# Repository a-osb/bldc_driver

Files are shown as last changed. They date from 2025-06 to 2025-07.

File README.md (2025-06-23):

# BLDC Motor Driver
  
This project aims to provide a compact and efficient solution for controlling brushless DC motors in robotics applications. It offers precise feedback and control, making it suitable for tasks that require accurate positioning and smooth motion.

Designed to be compatible with the SimpleFOC project

Based on key components
- DRV8317 integrated mosfet BLDC driver
- STM32G0 Microcontroller
- AS5047D magnetic encoder

Interfaces
- UART
- USB
- CAN

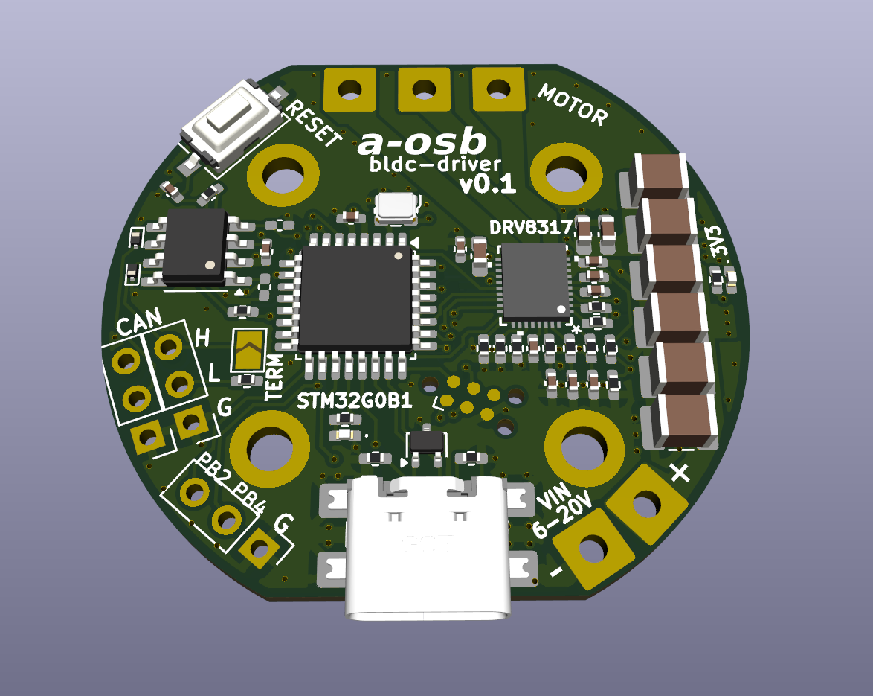
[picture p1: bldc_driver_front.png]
3D Front

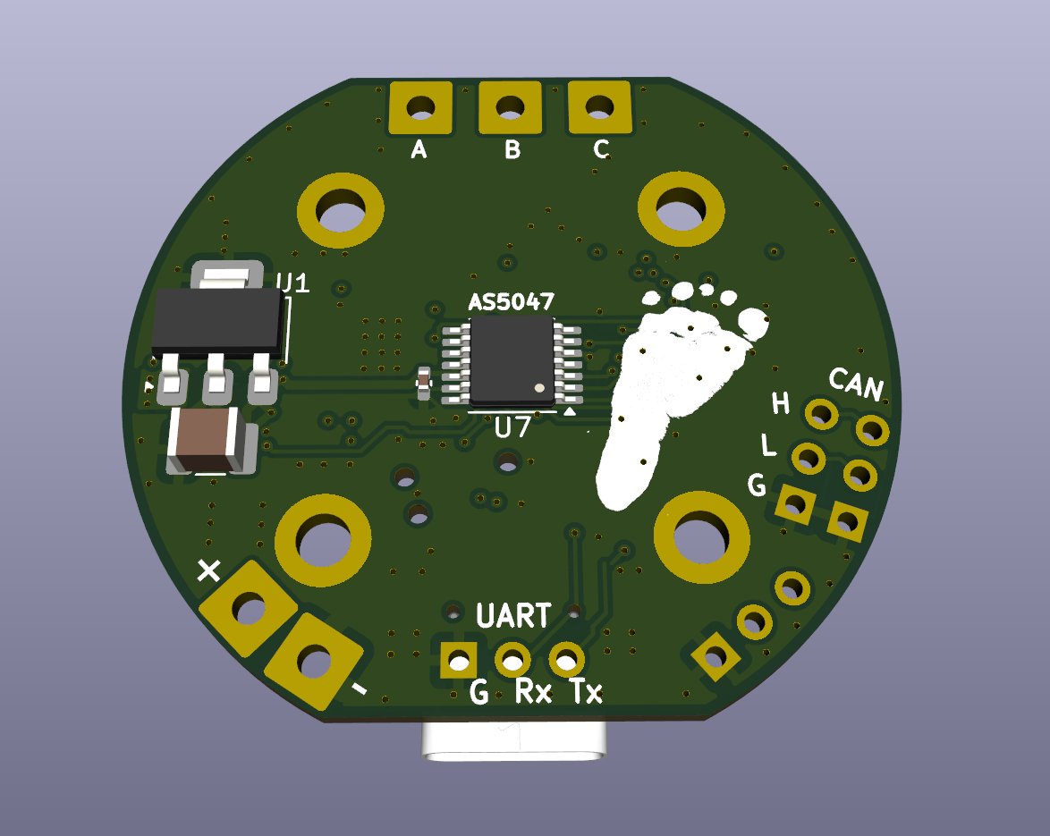
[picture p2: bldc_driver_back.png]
3D Back


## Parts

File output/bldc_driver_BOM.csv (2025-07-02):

Reference | Qty | Value | Rating | DNP | Exclude from BOM | Exclude from Board | Footprint | Datasheet
C1 | 1 | 10u | 50V |  |  |  | Capacitor_SMD:C_1210_3225Metric_Pad1.33x2.70mm_HandSolder | ~
C2 | 1 | 10u | 50V |  |  |  | Capacitor_SMD:C_1210_3225Metric_Pad1.33x2.70mm_HandSolder | ~
C3 | 1 | 10u | 50V |  |  |  | Capacitor_SMD:C_1210_3225Metric_Pad1.33x2.70mm_HandSolder | ~
C4 | 1 | 10u | 50V |  |  |  | Capacitor_SMD:C_1210_3225Metric_Pad1.33x2.70mm_HandSolder | ~
C5 | 1 | 10u | 50V |  |  |  | Capacitor_SMD:C_1210_3225Metric_Pad1.33x2.70mm_HandSolder | ~
C6 | 1 | 10u | 50V |  |  |  | Capacitor_SMD:C_1210_3225Metric_Pad1.33x2.70mm_HandSolder | ~
C7 | 1 | 100n | 6.3V |  |  |  | Capacitor_SMD:C_0402_1005Metric_Pad0.74x0.62mm_HandSolder | ~
C8 | 1 | 10u | 50V |  |  |  | Capacitor_SMD:C_1210_3225Metric_Pad1.33x2.70mm_HandSolder | ~
C9 | 1 | 100n |  | DNP |  |  | Capacitor_SMD:C_0402_1005Metric_Pad0.74x0.62mm_HandSolder | ~
C10 | 1 | 100n |  | DNP |  |  | Capacitor_SMD:C_0402_1005Metric_Pad0.74x0.62mm_HandSolder | ~
C11 | 1 | 100n | 6.3V |  |  |  | Capacitor_SMD:C_0402_1005Metric_Pad0.74x0.62mm_HandSolder | ~
C12 | 1 | 100n | 6.3V |  |  |  | Capacitor_SMD:C_0402_1005Metric_Pad0.74x0.62mm_HandSolder | ~
C14 | 1 | 100n | 6.3V |  |  |  | Capacitor_SMD:C_0402_1005Metric_Pad0.74x0.62mm_HandSolder | ~
C15 | 1 | 100n | 6.3V |  |  |  | Capacitor_SMD:C_0402_1005Metric_Pad0.74x0.62mm_HandSolder | ~
C16 | 1 | 100n | 6.3V |  |  |  | Capacitor_SMD:C_0402_1005Metric_Pad0.74x0.62mm_HandSolder | ~
C17 | 1 | 100n | 6.3V |  |  |  | Capacitor_SMD:C_0402_1005Metric_Pad0.74x0.62mm_HandSolder | ~
C_AVDD1 | 1 | 2.2u | 6.3V |  |  |  | Capacitor_SMD:C_0603_1608Metric_Pad1.08x0.95mm_HandSolder | ~
C_CP1 | 1 | 1u | 16V |  |  |  | Capacitor_SMD:C_0402_1005Metric_Pad0.74x0.62mm_HandSolder | ~
C_CSAREF1 | 1 | 100n | 6.3V |  |  |  | Capacitor_SMD:C_0402_1005Metric_Pad0.74x0.62mm_HandSolder | ~
C_FLY1 | 1 | 100n | 50V |  |  |  | Capacitor_SMD:C_0402_1005Metric_Pad0.74x0.62mm_HandSolder | ~
C_VIN_AVDD1 | 1 | 100n | 50V |  |  |  | Capacitor_SMD:C_0402_1005Metric_Pad0.74x0.62mm_HandSolder | ~
C_VIN_AVDD2 | 1 | 10u | 50V |  |  |  | Capacitor_SMD:C_0805_2012Metric_Pad1.18x1.45mm_HandSolder | ~
C_VM1 | 1 | 100n | 50V |  |  |  | Capacitor_SMD:C_0402_1005Metric_Pad0.74x0.62mm_HandSolder | ~
C_VM2 | 1 | 10u | 50V |  |  |  | Capacitor_SMD:C_0805_2012Metric_Pad1.18x1.45mm_HandSolder | ~
D1 | 1 | ESD9B3.3ST5G |  |  |  |  | Diode_SMD:D_SOD-923 | https://www.onsemi.com/pub/Collateral/ESD9B-D.PDF
D2 | 1 | ESD9B3.3ST5G |  |  |  |  | Diode_SMD:D_SOD-923 | https://www.onsemi.com/pub/Collateral/ESD9B-D.PDF
D3 | 1 | LED |  |  |  |  | LED_SMD:LED_0402_1005Metric_Pad0.77x0.64mm_HandSolder | ~
D4 | 1 | LED |  |  |  |  | LED_SMD:LED_0402_1005Metric_Pad0.77x0.64mm_HandSolder | ~
J2 | 1 | USB_C_Receptacle_USB2.0_16P |  |  |  |  | bldc_driver:USB_C_Receptacle_GCT_USB4110 | https://www.usb.org/sites/default/files/documents/usb_type-c.zip
R1 | 1 | 5.1k |  |  |  |  | Resistor_SMD:R_0402_1005Metric_Pad0.72x0.64mm_HandSolder | ~
R2 | 1 | 5.1k |  |  |  |  | Resistor_SMD:R_0402_1005Metric_Pad0.72x0.64mm_HandSolder | ~
R3 | 1 | 5.1k |  |  |  |  | Resistor_SMD:R_0402_1005Metric_Pad0.72x0.64mm_HandSolder | ~
R4 | 1 | 5.1k |  |  |  |  | Resistor_SMD:R_0402_1005Metric_Pad0.72x0.64mm_HandSolder | ~
R5 | 1 | 1k |  |  |  |  | Resistor_SMD:R_0402_1005Metric_Pad0.72x0.64mm_HandSolder | ~
R6 | 1 | 1k |  |  |  |  | Resistor_SMD:R_0402_1005Metric_Pad0.72x0.64mm_HandSolder | ~
R7 | 1 | 120R |  |  |  |  | Resistor_SMD:R_0402_1005Metric_Pad0.72x0.64mm_HandSolder | ~
R8 | 1 | 120R |  |  |  |  | Resistor_SMD:R_0402_1005Metric_Pad0.72x0.64mm_HandSolder | ~
R9 | 1 | 120R |  |  |  |  | Resistor_SMD:R_0402_1005Metric_Pad0.72x0.64mm_HandSolder | ~
R11 | 1 | 5.1k |  |  |  |  | Resistor_SMD:R_0402_1005Metric_Pad0.72x0.64mm_HandSolder | ~
R12 | 1 | 100k |  |  |  |  | Resistor_SMD:R_0402_1005Metric_Pad0.72x0.64mm_HandSolder | ~
R_GAIN1 | 1 | 0R |  |  |  |  | Resistor_SMD:R_0402_1005Metric_Pad0.72x0.64mm_HandSolder | ~
R_MODE1 | 1 | 0R |  |  |  |  | Resistor_SMD:R_0402_1005Metric_Pad0.72x0.64mm_HandSolder | ~
R_nFault1 | 1 | 5.1k |  |  |  |  | Resistor_SMD:R_0402_1005Metric_Pad0.72x0.64mm_HandSolder | ~
R_nSLEEP1 | 1 | 5.1k |  |  |  |  | Resistor_SMD:R_0402_1005Metric_Pad0.72x0.64mm_HandSolder | ~
R_SLEW1 | 1 | 0R |  |  |  |  | Resistor_SMD:R_0402_1005Metric_Pad0.72x0.64mm_HandSolder | ~
R_term1 | 1 | 120R |  |  |  |  | Resistor_SMD:R_0402_1005Metric_Pad0.72x0.64mm_HandSolder | ~
SW1 | 1 | SW_Push |  |  |  |  | Button_Switch_SMD:SW_Push_1P1T_NO_CK_KMR2 | ~
U1 | 1 | UA78M33QDCYRG4Q1 |  |  |  |  | Package_TO_SOT_SMD:SOT-223-3_TabPin2 | https://www.ti.com/lit/gpn/UA78M-Q1
U2 | 1 | SN65HVD230 |  |  |  |  | Package_SO:SOIC-8_3.9x4.9mm_P1.27mm | http://www.ti.com/lit/ds/symlink/sn65hvd230.pdf
U3 | 1 | TPD2E2U06DCK |  |  |  |  | Package_TO_SOT_SMD:SOT-323_SC-70 | http://www.ti.com/lit/ds/symlink/tpd2e2u06.pdf
U5 | 1 | STM32G0B1KCTx |  |  |  |  | Package_QFP:LQFP-32_7x7mm_P0.8mm | https://www.st.com/resource/en/datasheet/stm32g0b1kc.pdf
U6 | 1 | DRV8317HREER |  |  |  |  | bldc_driver:WQFN36_REE_TEX | DRV8317HREER
U7 | 1 | AS5047D |  |  |  |  | Package_SO:TSSOP-14_4.4x5mm_P0.65mm | https://ams.com/documents/20143/36005/AS5047D_DS000394_2-00.pdf
Y1 | 1 | ECS-2520MV-160-CN |  |  |  |  | bldc_driver:Oscillator_SMD_ECS_2520MV-xxx-xx-4Pin_2.5x2.0mm | https://www.ecsxtal.com/store/pdf/ECS-2520MV.pdf

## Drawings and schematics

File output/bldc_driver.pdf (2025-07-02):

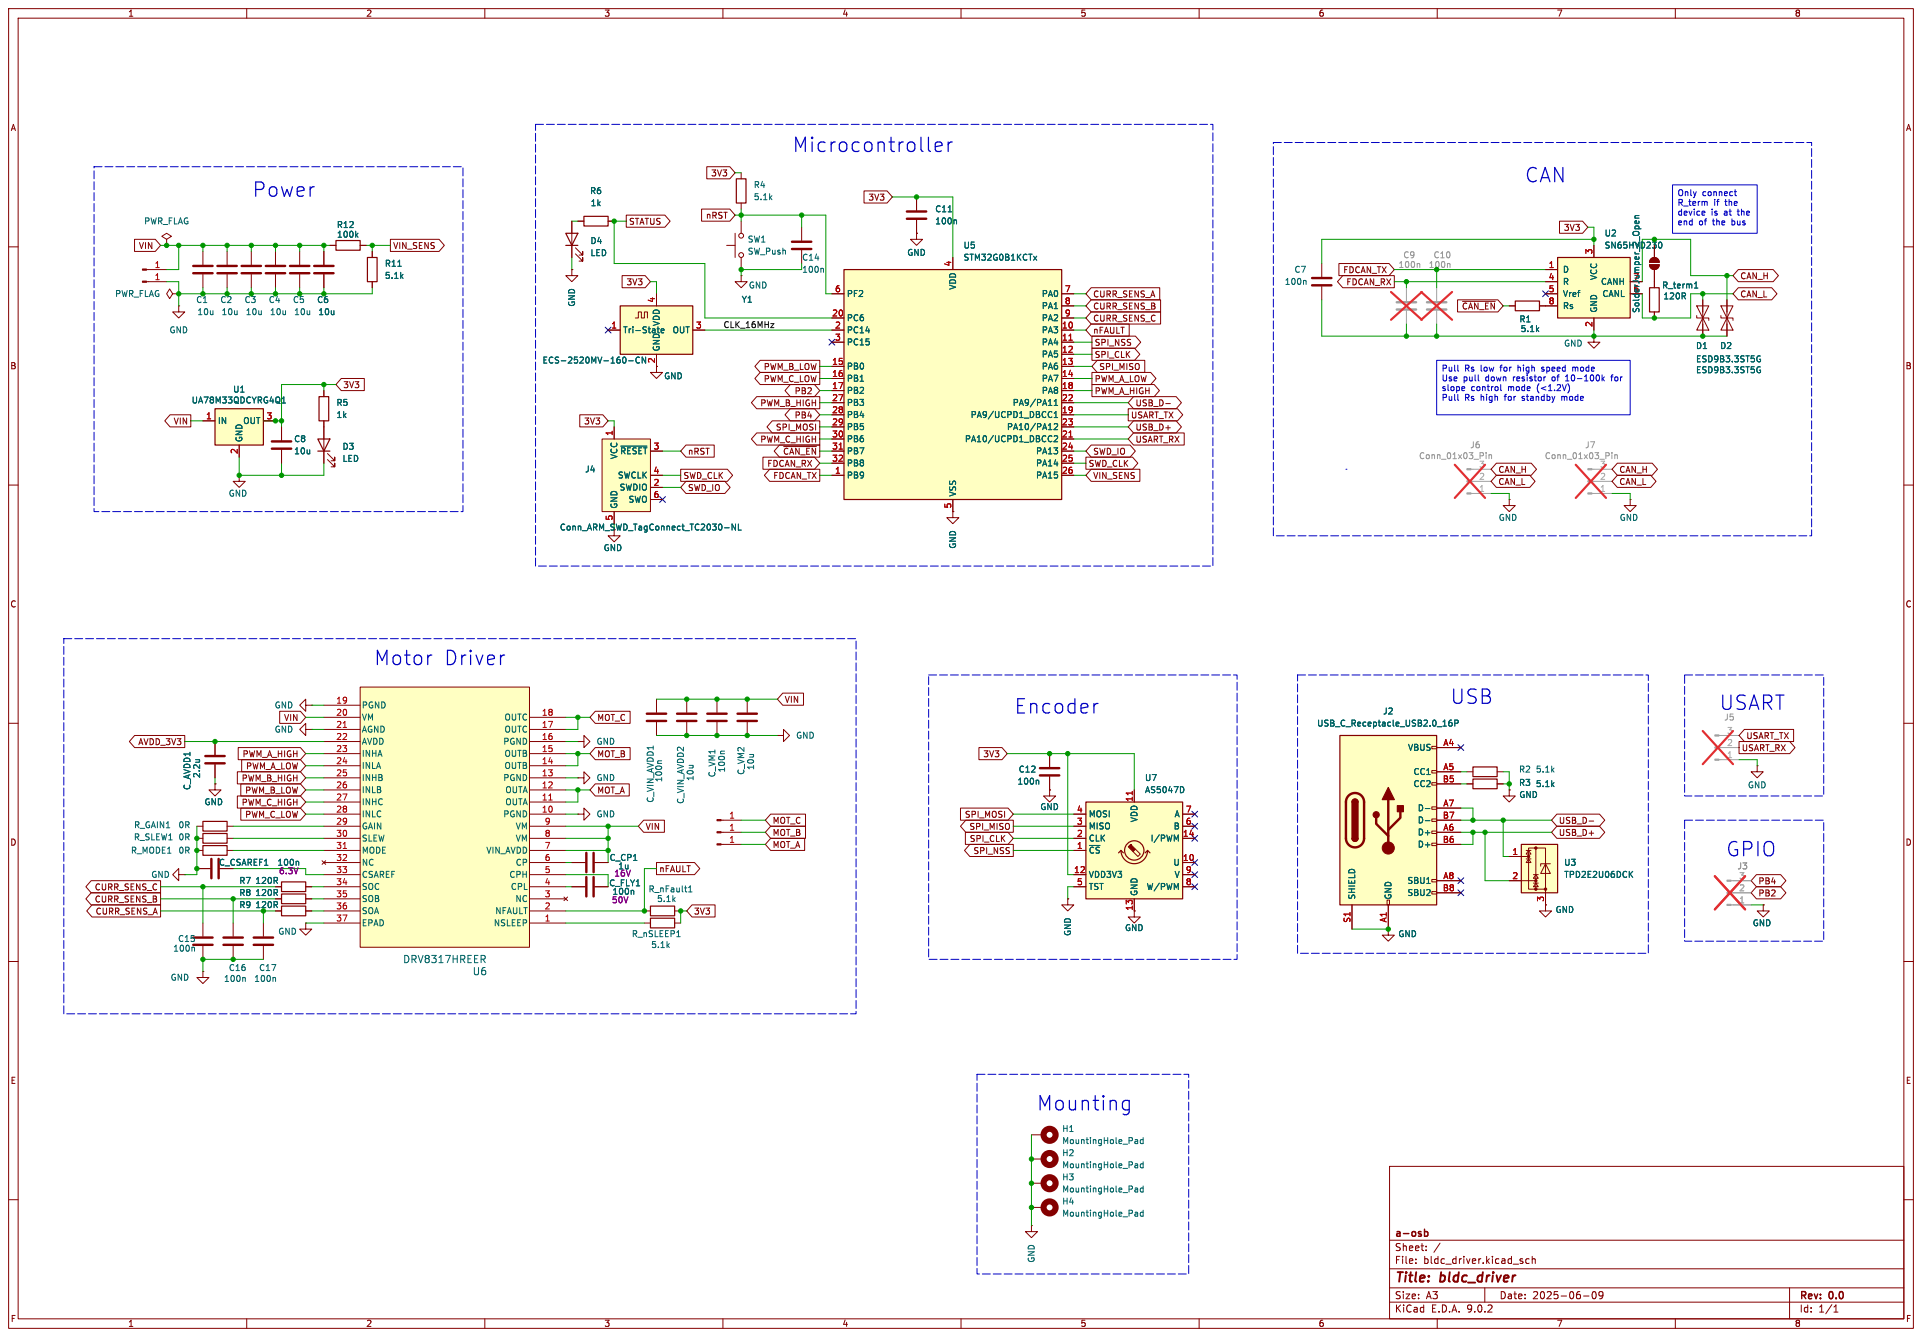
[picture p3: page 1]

device is at the

5 ~{RESET}3 SWCLK 4 SWDIO 2 SWO 6 D4

5 ~{RESET}3 SWCLK 4 SWDIO 2 SWO 6

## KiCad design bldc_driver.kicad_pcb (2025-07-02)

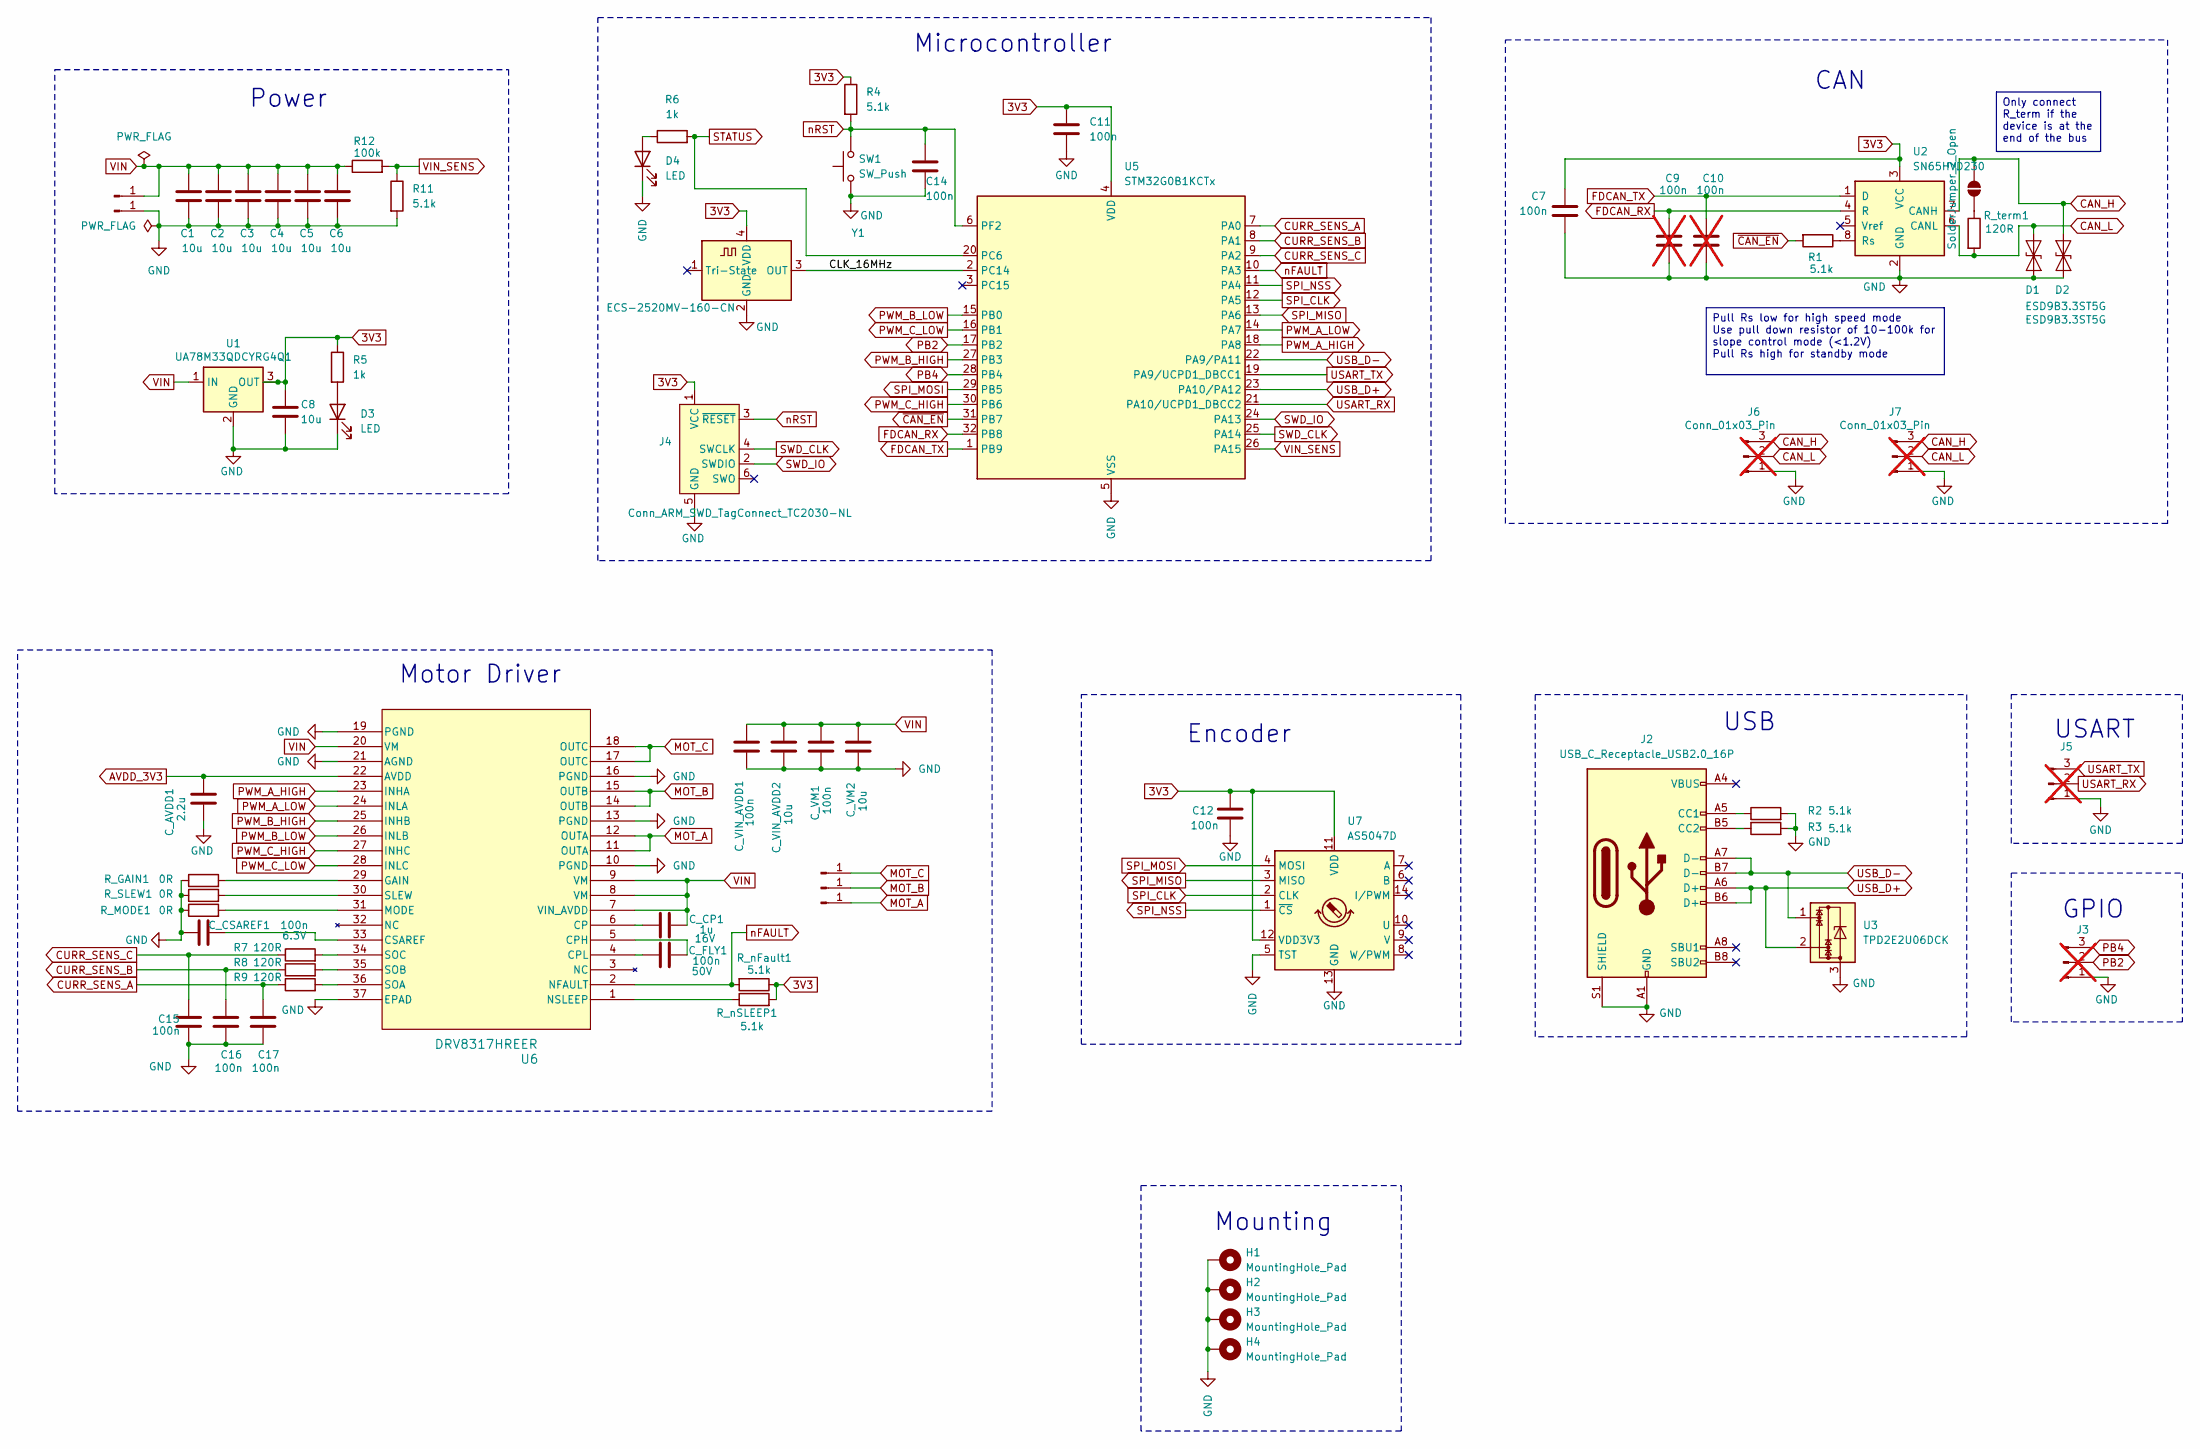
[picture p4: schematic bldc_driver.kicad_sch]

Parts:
C1, C2, C3, C4, C5, C6, C8: 10u; C_1210_3225Metric_Pad1.33x2.70mm_HandSolder; Rating 50V
C7, C11, C12, C14, C15, C16, C17: 100n; C_0402_1005Metric_Pad0.74x0.62mm_HandSolder; Rating 6.3V
C9, C10: 100n; C_0402_1005Metric_Pad0.74x0.62mm_HandSolder; not fitted
C_AVDD1: 2.2u; C_0603_1608Metric_Pad1.08x0.95mm_HandSolder; Rating 6.3V
C_CP1: 1u; C_0402_1005Metric_Pad0.74x0.62mm_HandSolder; Rating 16V
C_CSAREF1: 100n; C_0402_1005Metric_Pad0.74x0.62mm_HandSolder; Rating 6.3V
C_FLY1: 100n; C_0402_1005Metric_Pad0.74x0.62mm_HandSolder; Rating 50V
C_VIN_AVDD1: 100n; C_0402_1005Metric_Pad0.74x0.62mm_HandSolder; Rating 50V
C_VIN_AVDD2: 10u; C_0805_2012Metric_Pad1.18x1.45mm_HandSolder; Rating 50V
C_VM1: 100n; C_0402_1005Metric_Pad0.74x0.62mm_HandSolder; Rating 50V
C_VM2: 10u; C_0805_2012Metric_Pad1.18x1.45mm_HandSolder; Rating 50V
D1, D2: ESD9B3.3ST5G; D_SOD-923
D3, D4: LED; LED_0402_1005Metric_Pad0.77x0.64mm_HandSolder
H1, H2, H3, H4: MountingHole_Pad; MountingHole_2.7mm_M2.5_DIN965_Pad_TopBottom
J1, J8, J9, J10, J11: Conn_01x01_Pin; SolderWire-0.75sqmm_1x01_D1.25mm_OD3.5mm
J2: USB_C_Receptacle_USB2.0_16P; USB_C_Receptacle_GCT_USB4110
J3, J5, J6, J7: Conn_01x03_Pin; PinHeader_1x03_P2.54mm_Vertical; not fitted
J4: Conn_ARM_SWD_TagConnect_TC2030-NL; Tag-Connect_TC2030-IDC-NL_2x03_P1.27mm_Vertical
JP1: SolderJumper_2_Open; SolderJumper-2_P1.3mm_Open_TrianglePad1.0x1.5mm
R1, R2, R3, R4, R11: 5.1k; R_0402_1005Metric_Pad0.72x0.64mm_HandSolder
R5, R6: 1k; R_0402_1005Metric_Pad0.72x0.64mm_HandSolder
R7, R8, R9: 120R; R_0402_1005Metric_Pad0.72x0.64mm_HandSolder
R12: 100k; R_0402_1005Metric_Pad0.72x0.64mm_HandSolder
R_GAIN1: 0R; R_0402_1005Metric_Pad0.72x0.64mm_HandSolder
R_MODE1: 0R; R_0402_1005Metric_Pad0.72x0.64mm_HandSolder
R_SLEW1: 0R; R_0402_1005Metric_Pad0.72x0.64mm_HandSolder
R_nFault1: 5.1k; R_0402_1005Metric_Pad0.72x0.64mm_HandSolder
R_nSLEEP1: 5.1k; R_0402_1005Metric_Pad0.72x0.64mm_HandSolder
R_term1: 120R; R_0402_1005Metric_Pad0.72x0.64mm_HandSolder
SW1: SW_Push; SW_Push_1P1T_NO_CK_KMR2
U1: UA78M33QDCYRG4Q1; SOT-223-3_TabPin2
U2: SN65HVD230; SOIC-8_3.9x4.9mm_P1.27mm
U3: TPD2E2U06DCK; SOT-323_SC-70
U5: STM32G0B1KCTx; LQFP-32_7x7mm_P0.8mm
U6: DRV8317HREER; WQFN36_REE_TEX
U7: AS5047D; TSSOP-14_4.4x5mm_P0.65mm
Y1: ECS-2520MV-160-CN; Oscillator_SMD_ECS_2520MV-xxx-xx-4Pin_2.5x2.0mm

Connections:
3V3: C7.1, C8.1, C11.1, C12.1, J4.1 (VCC), R4.1, R5.1, R_nFault1.1, R_nSLEEP1.2, U1.3 (OUT), U2.3 (VCC), U5.4 (VDD), U7.11 (VDD), U7.12 (VDD3V3), Y1.4 (VDD)
/CLK_16MHz: U5.2 (PC14), Y1.3 (OUT)
AVDD_3V3: C_AVDD1.2, U6.22 (AVDD)
CAN_H: D2.2 (A2), J6.3, J7.3, JP1.2 (B), U2.7 (CANH)
CAN_L: D1.2 (A2), J6.2, J7.2, R_term1.2, U2.6 (CANL)
CURR_SENS_A: C17.1, R9.1, U5.7 (PA0)
CURR_SENS_B: C16.1, R8.1, U5.8 (PA1)
CURR_SENS_C: C15.1, R7.1, U5.9 (PA2)
FDCAN_RX: C9.1, U2.4 (R), U5.32 (PB8)
FDCAN_TX: C10.1, U2.1 (D), U5.1 (PB9)
GND: C1.2, C2.2, C3.2, C4.2, C5.2, C6.2, C7.2, C8.2, C9.2, C10.2, C11.2, C12.2, C14.2, C15.2, C16.2, C17.2, C_AVDD1.1, C_CSAREF1.1, C_VIN_AVDD1.2, C_VIN_AVDD2.1, C_VM1.2, C_VM2.2, D1.1 (A1), D2.1 (A1), D3.1 (K), D4.1 (K), H1.1, H2.1, H3.1, H4.1, J1.1, J2.A1 (GND), J2.A12 (GND), J2.B1 (GND), J2.B12 (GND), J2.S1 (SHIELD), J3.1, J4.5 (GND), J5.1, J6.1, J7.1, R2.2, R3.2, R11.2, R_GAIN1.1, R_MODE1.1, R_SLEW1.1, SW1.1, U1.2 (GND), U2.2 (GND), U3.3, U5.5 (VSS), U6.10 (PGND), U6.13 (PGND), U6.16 (PGND), U6.19 (PGND), U6.21 (AGND), U6.37 (EPAD), U7.5 (TST), U7.13 (GND), Y1.2 (GND)
MOT_A: J8.1, U6.11 (OUTA), U6.12 (OUTA)
MOT_B: J9.1, U6.14 (OUTB), U6.15 (OUTB)
MOT_C: J10.1, U6.17 (OUTC), U6.18 (OUTC)
unnamed: D3.2 (A), R5.2
unnamed: D4.2 (A), R6.1
unnamed: J2.A5 (CC1), R2.1
unnamed: J2.B5 (CC2), R3.1
unnamed: JP1.1 (A), R_term1.1
unnamed: R1.1, U2.8 (Rs)
unnamed: C_CP1.1, U6.6 (CP)
unnamed: C_FLY1.2, U6.5 (CPH)
unnamed: C_FLY1.1, U6.4 (CPL)
unnamed: C_CSAREF1.2, U6.33 (CSAREF)
unnamed: R_GAIN1.2, U6.29 (GAIN)
unnamed: R_MODE1.2, U6.31 (MODE)
unnamed: R_nSLEEP1.1, U6.1 (NSLEEP)
unnamed: R_SLEW1.2, U6.30 (SLEW)
unnamed: R9.2, U6.36 (SOA)
unnamed: R8.2, U6.35 (SOB)
unnamed: R7.2, U6.34 (SOC)
PB2: J3.2, U5.17 (PB2)
PB4: J3.3, U5.28 (PB4)
PWM_A_HIGH: U5.18 (PA8), U6.23 (INHA)
PWM_A_LOW: U5.14 (PA7), U6.24 (INLA)
PWM_B_HIGH: U5.27 (PB3), U6.25 (INHB)
PWM_B_LOW: U5.15 (PB0), U6.26 (INLB)
PWM_C_HIGH: U5.30 (PB6), U6.27 (INHC)
PWM_C_LOW: U5.16 (PB1), U6.28 (INLC)
SPI_CLK: U5.12 (PA5), U7.2 (CLK)
SPI_MISO: U5.13 (PA6), U7.3 (MISO)
SPI_MOSI: U5.29 (PB5), U7.4 (MOSI)
SPI_NSS: U5.11 (PA4), U7.1 (~CS)
STATUS: R6.2, U5.20 (PC6)
SWD_CLK: J4.4 (SWCLK), U5.25 (PA14)
SWD_IO: J4.2 (SWDIO), U5.24 (PA13)
USART_RX: J5.2, U5.21 (PA10/UCPD1_DBCC2)
USART_TX: J5.3, U5.19 (PA9/UCPD1_DBCC1)
USB_D+: J2.A6 (D+), J2.B6 (D+), U3.2, U5.23 (PA10/PA12)
USB_D-: J2.A7 (D-), J2.B7 (D-), U3.1, U5.22 (PA9/PA11)
VIN: C1.1, C2.1, C3.1, C4.1, C5.1, C6.1, C_CP1.2, C_VIN_AVDD1.1, C_VIN_AVDD2.2, C_VM1.1, C_VM2.1, J11.1, R12.1, U1.1 (IN), U6.7 (VIN_AVDD), U6.8 (VM), U6.9 (VM), U6.20 (VM)
VIN_SENS: R11.1, R12.2, U5.26 (PA15)
nFAULT: R_nFault1.2, U5.10 (PA3), U6.2 (NFAULT)
nRST: C14.1, J4.3 (~RESET), R4.2, SW1.2, U5.6 (PF2)
~CAN_EN: R1.2, U5.31 (PB7)

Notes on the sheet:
Encoder
USART
USB
CAN
GPIO
Mounting
Motor Driver
Microcontroller
Power
Pull Rs low for high speed mode Use pull down resistor of 10-100k for slope control mode (<1.2V) Pull Rs high for standby mode
Only connect R_term if the device is at the end of the bus

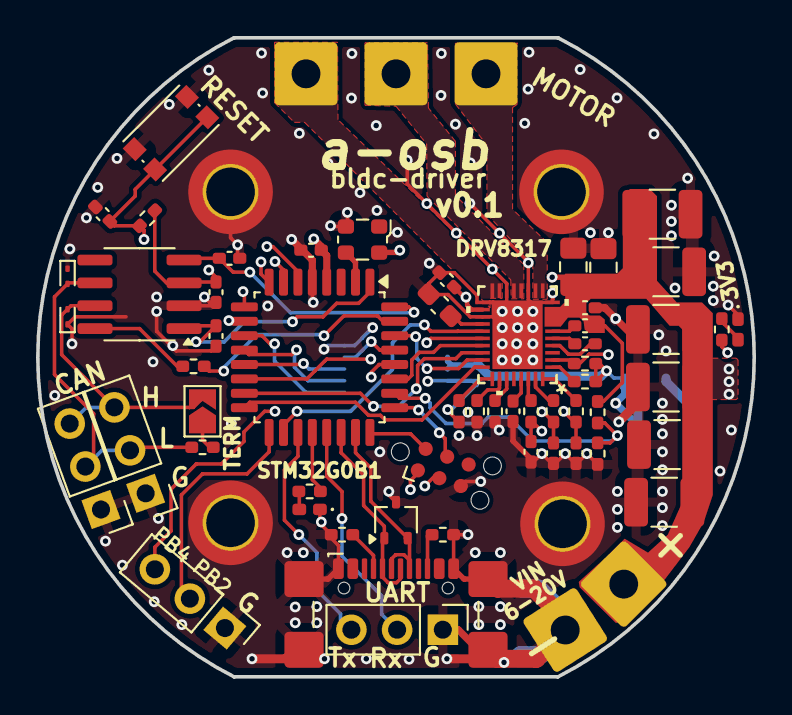
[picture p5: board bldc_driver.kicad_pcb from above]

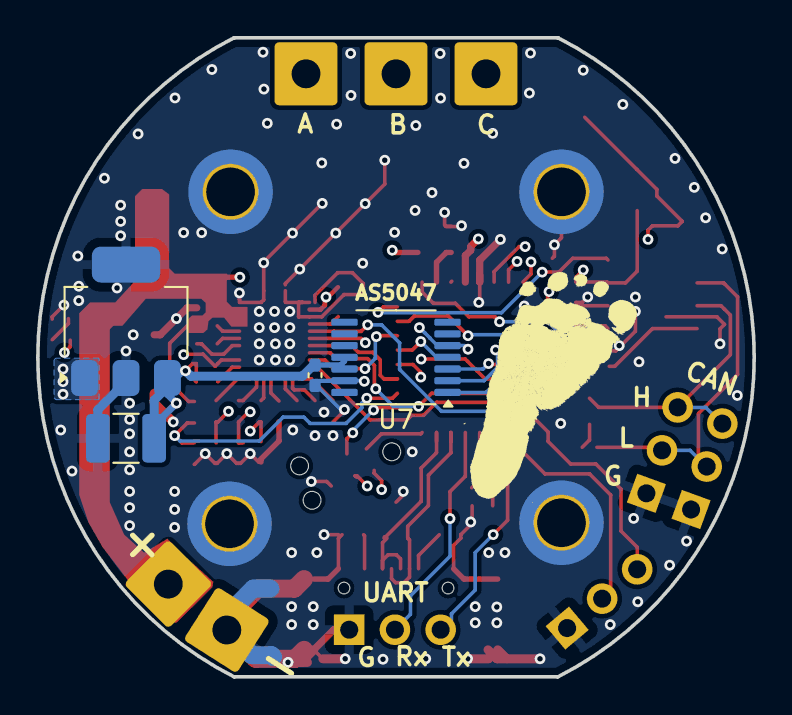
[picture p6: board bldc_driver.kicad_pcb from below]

Board: 4 copper layers, 39.8 x 35.5 mm, 69 parts (4 on the bottom side), 55 nets.

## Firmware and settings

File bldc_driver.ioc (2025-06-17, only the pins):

Mcu.UserName=STM32G0B1KCTx
PA0.Signal=ADC1_IN0
PA1.Signal=ADC1_IN1
PA10.Signal=USART1_RX
PA13.Signal=SYS_SWDIO
PA14-BOOT0.Signal=SYS_SWCLK
PA2.Signal=ADC1_IN2
PA4.Signal=SPI1_NSS
PA5.Signal=SPI1_SCK
PA6.Signal=SPI1_MISO
PA7.Signal=TIM1_CH1N
PA8.Signal=S_TIM1_CH1
PA9.Signal=USART1_TX
PB0.Signal=TIM1_CH2N
PB1.Signal=TIM1_CH3N
PB3.Signal=S_TIM1_CH2
PB5.Signal=SPI1_MOSI
PB6.Signal=S_TIM1_CH3
PB7.GPIO_Label=CAN_EN
PB7.Signal=GPIO_Output
PB8.Signal=FDCAN1_RX
PB9.Signal=FDCAN1_TX
PC6.GPIO_Label=STATUS
PC6.Signal=GPIO_Output

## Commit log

2025-05-02 Added initial cube mx and kicad proj
    [bldc_driver.kicad_pcb, bldc_driver.kicad_sch]
2025-05-21 progress on schematic for DRV8317H
    [bldc_driver.kicad_sch]
2025-06-03 initial placement of componeents
    [bldc_driver.kicad_pcb, bldc_driver.kicad_sch]
2025-06-17 schematic and layout mostly done
    [bldc_driver.kicad_pcb, bldc_driver.kicad_sch]
2025-06-19 for review with outputs
    [bldc_driver-B_Cu.gbr, bldc_driver-B_Mask.gbr, bldc_driver-B_Paste.gbr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]
2025-06-23 drc checked
    [bldc_driver-B_Cu.gbr, bldc_driver-B_Mask.gbr, bldc_driver-B_Paste.gbr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]
2025-06-23 BOM with ratings
    [bldc_driver.kicad_sch, bldc_driver_BOM.csv]
2025-06-23 added pos files
    [bldc_driver-bottom-pos.csv, bldc_driver-top-pos.csv]
2025-07-02 cut rev 0.1
    [bldc_driver-B_Cu.gbr, bldc_driver-B_Mask.gbr, bldc_driver-B_Paste.gbr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]
